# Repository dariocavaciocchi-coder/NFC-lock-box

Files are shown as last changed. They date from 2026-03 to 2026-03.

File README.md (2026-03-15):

# NFC-lock-box

Description:

My project is a lock box that uses rfid/NFC technology to lock and unlock it. It also has an LED to show whether it is locked or unlocked. All you have to do is tap the accepted card and the servo moves to unlock it, remove the lid, take stuff out or put stuff in, close it and tap the card again and the servo will lock the box. I made this project so I could store my most delicate items, without the risk of other people breaking them, as it has happened multiple times before (not on purpose).

Struggles:

I had a few struggles while making this project, but I will only talk about the big one, as I don’t want to bore you. I found it very hard to find an effective way to lock and unlock the box effectively, so much so that I changed the mechanism multiple times. At first, I had it to where a servo arm would go in a hole with a wedge and would move to lock/unlock but realised it would be hard to track the circular motion inside that hole, so then I thought of doing a linear locking mechanism. I came up with many ideas, but decided to go with a rack and pinion, as I thought that would be the easiest to implement in the box. I found a template for a rack and pinion online and modified it, so it could fit into the design of my box.

BOM:

A more detailed BOM can be found in the BOM folder

* Xiao RP2040 module X1
* RC522 module set X1
* SG90 servo motor X1
* 3D printed box X1
* M3 Headset inserts X6
* M3 4mm spacer X8
* PCB X1
* LED X1
* 330ohm resistor X1
* 100nF ceramic capacitor X1
* 100microF electrolytic capacitor X1
* 2.54mm pin header X3
* M3 12mm screws X4
* M3 6mm screws X2

Images:

More images can be found in the images folder

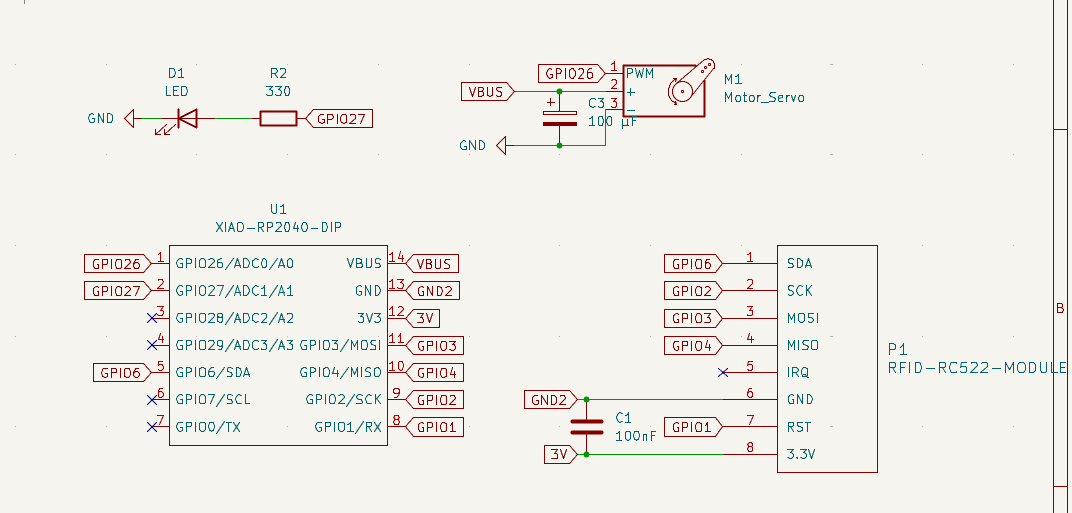
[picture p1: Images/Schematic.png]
Schematic


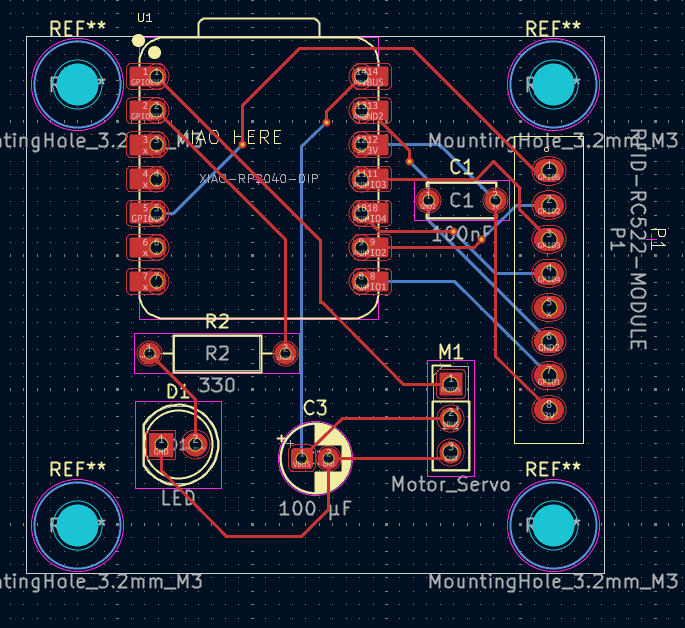
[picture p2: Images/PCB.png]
PCB


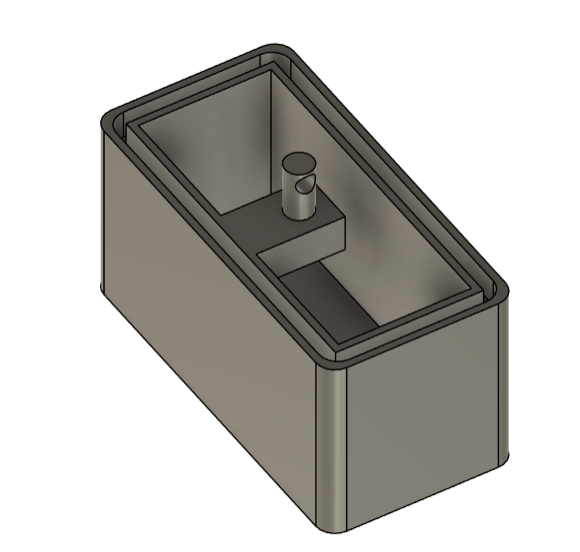
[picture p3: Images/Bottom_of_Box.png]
Bottom Case

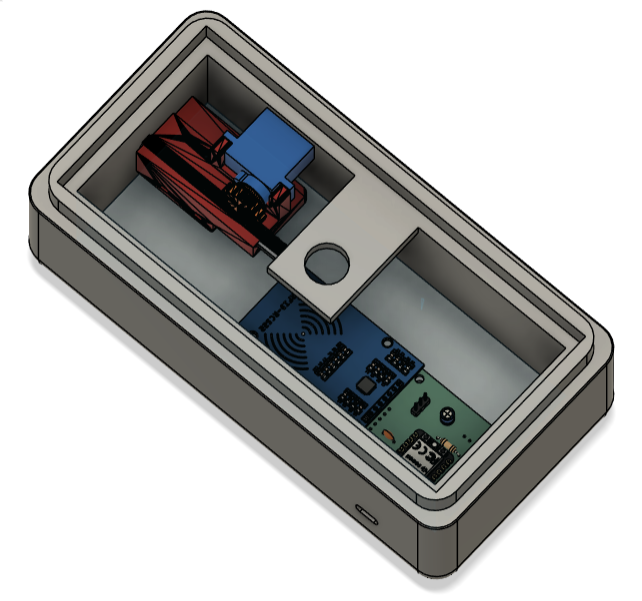
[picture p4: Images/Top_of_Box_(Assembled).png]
Top Case

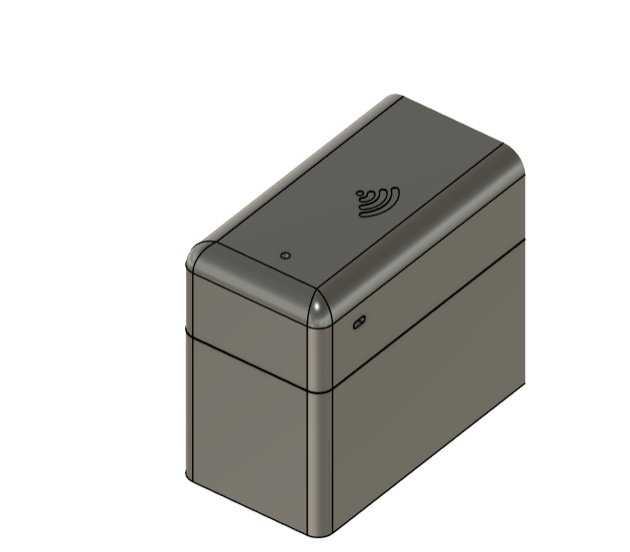
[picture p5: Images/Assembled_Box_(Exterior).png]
Assembled


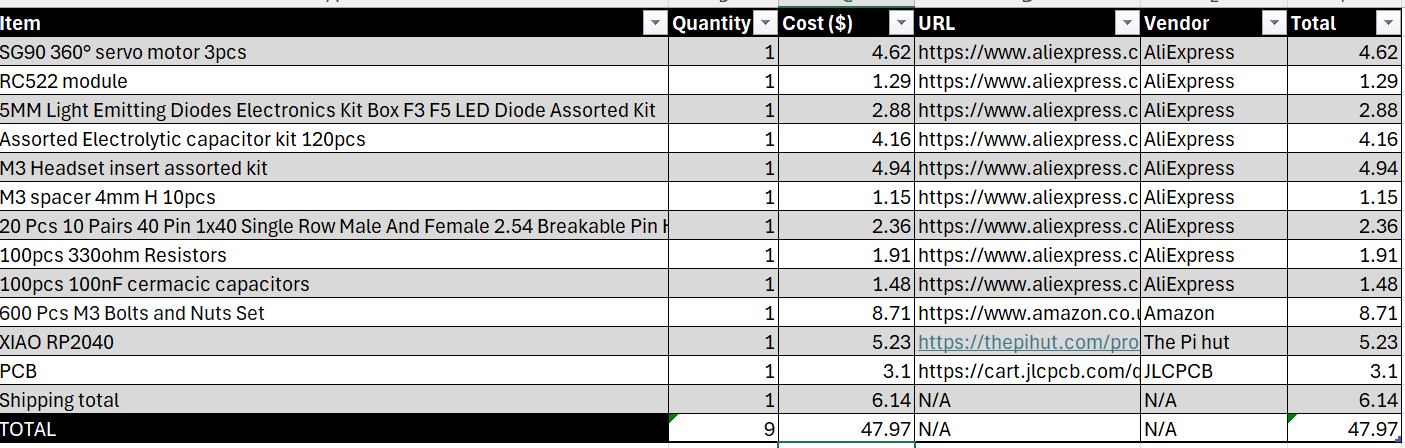
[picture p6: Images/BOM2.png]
BOM


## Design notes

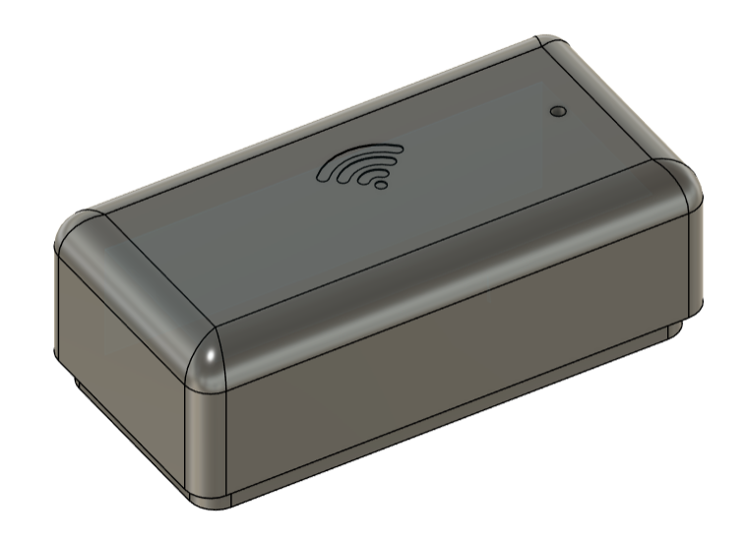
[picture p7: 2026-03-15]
Images/Top_of_Box_(Top).png

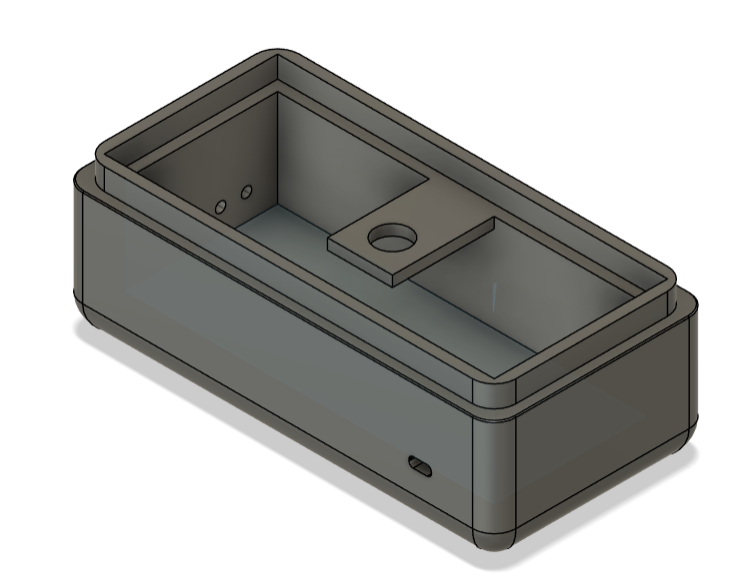
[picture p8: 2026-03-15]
Images/Top_of_Box_(Bottom).png

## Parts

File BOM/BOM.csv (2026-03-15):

Item | Quantity | Cost ($) | URL | Vendor | Total
SG90 360° servo motor 3pcs | 1 | 4.62 | https://www.aliexpress.com/item/1005005310063582.html?curPageLogUid=5EMKYWtYPEn4 | AliExpress | 4.62
RC522 module | 1 | 1.29 | https://www.aliexpress.com/item/1005006441061112.html?curPageLogUid=9xwa73kRGVRp | AliExpress | 1.29
5MM Light Emitting Diodes Electronics Kit Box F3 F5 LED Diode Assorted Kit | 1 | 2.88 | https://www.aliexpress.com/item/1005004543292837.html?curPageLogUid=vBeAjtTDarnR | AliExpress | 2.88
Assorted Electrolytic capacitor kit 120pcs | 1 | 4.16 | https://www.aliexpress.com/item/1005005661484224.html?curPageLogUid=ZUkhXYdLh8eC | AliExpress | 4.16
M3 Headset insert assorted kit | 1 | 4.94 | https://www.aliexpress.com/item/1005006472962973.html?curPageLogUid=ni6CXoPvNdtc | AliExpress | 4.94
M3 spacer 4mm H 10pcs | 1 | 1.15 | https://www.aliexpress.com/item/1005006915134966.html?curPageLogUid=MaqOvrXhgtMa | AliExpress | 1.15
20 Pcs 10 Pairs 40 Pin 1x40 Single Row Male And Female 2.54 Breakable Pin Header PCB Connector Strip | 1 | 2.36 | https://www.aliexpress.com/item/1005008559565009.html?curPageLogUid=BqjJbkfmWVMf | AliExpress | 2.36
100pcs 330ohm Resistors | 1 | 1.91 | https://www.aliexpress.com/item/1005003923602966.html?curPageLogUid=jXFSVmhfiauj | AliExpress | 1.91
100pcs 100nF cermacic capacitors | 1 | 1.48 | https://www.aliexpress.com/item/1005002290441861.html?curPageLogUid=19AxGaqwAapf | AliExpress | 1.48
600 Pcs M3 Bolts and Nuts Set | 1 | 8.71 | https://www.amazon.co.uk/KOXXIAMOQ-Washers-Mechanical-Fastener-Assortment/dp/B0CJ6L82T8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 | Amazon | 8.71
XIAO RP2040 | 1 | 5.23 | https://thepihut.com/products/seeed-xiao-rp2040 | The Pi hut | 5.23
PCB | 1 | 3.1 | https://cart.jlcpcb.com/quote?spm=Jlcpcb.Homepage.1006&spm=Jlcpcb.Homepage.1006 | JLCPCB | 3.1
Shipping total | 1 | 6.14 | N/A | N/A | 6.14
TOTAL | 9 | 47.97 | N/A | N/A | 47.97

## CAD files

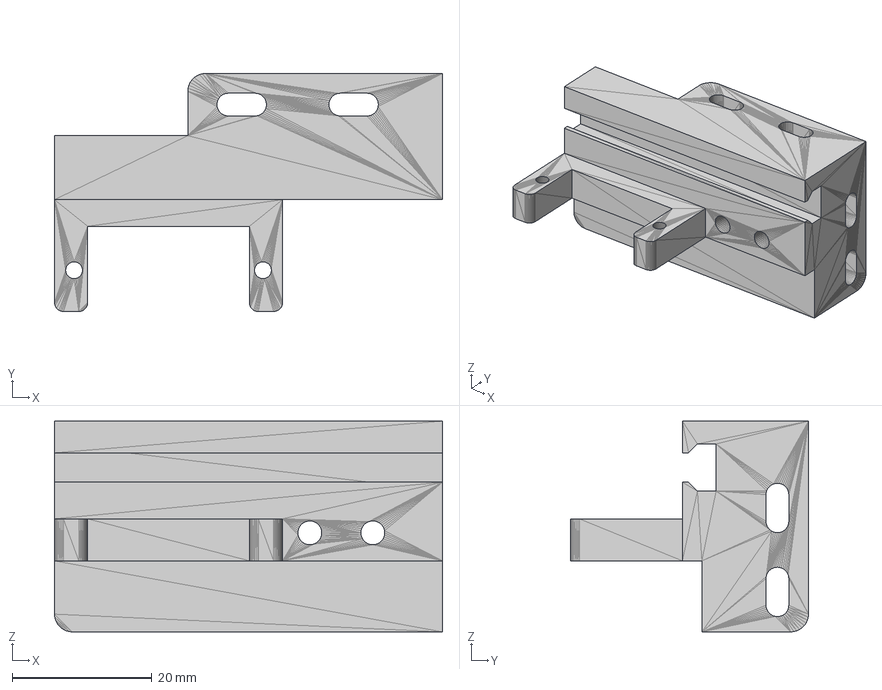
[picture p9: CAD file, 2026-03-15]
CAD/Motor_Bracket_Mini_Version.step
55.5 x 34.0 x 30.1 mm

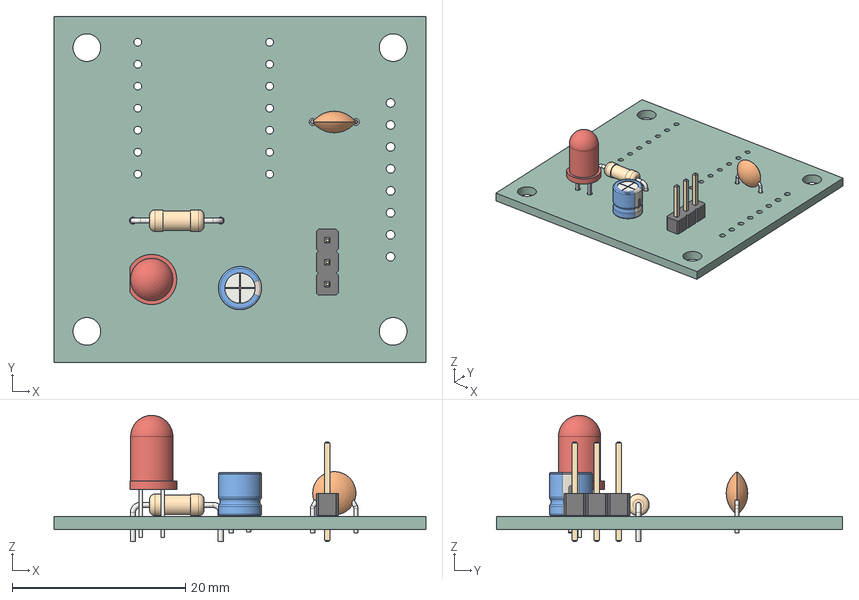
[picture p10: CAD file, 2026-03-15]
CAD/PCB.step
43.0 x 40.0 x 14.6 mm
PinHeader_1x03_P2.54mm_Vertical
LED_D5.0mm
C_Disc_D5.0mm_W2.5mm_P5.00mm
R_Axial_DIN0207_L6.3mm_D2.5mm_P10.16mm_Horizontal
CP_Radial_D5.0mm_P2.00mm
Lock box_PCB

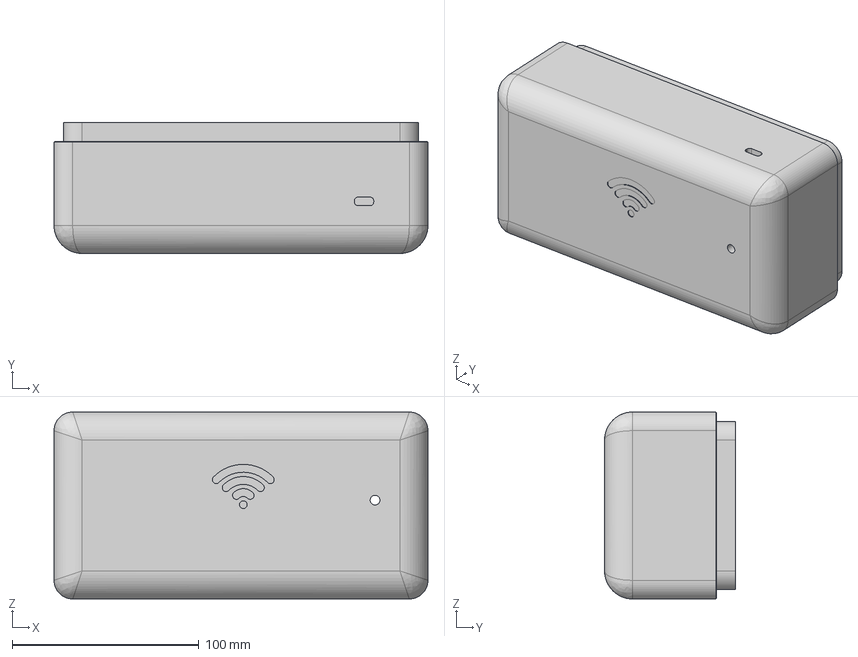
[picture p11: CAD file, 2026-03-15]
CAD/Top of box.step
200.0 x 70.0 x 100.0 mm

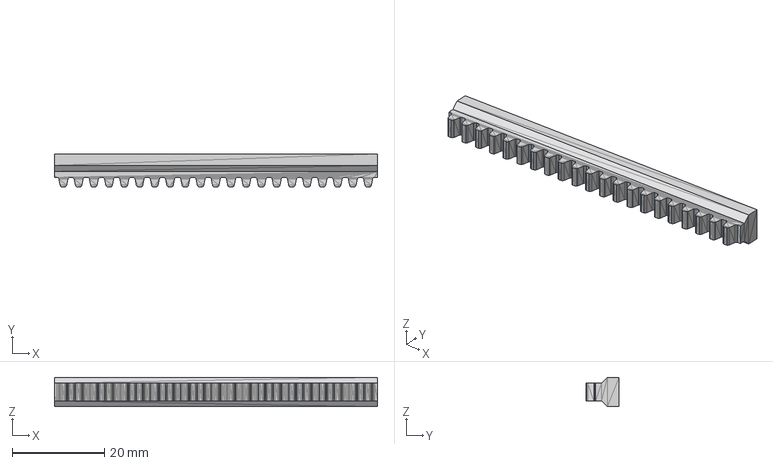
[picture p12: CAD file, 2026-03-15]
CAD/Pusher_75mm_Long.step
70.0 x 7.20 x 6.35 mm

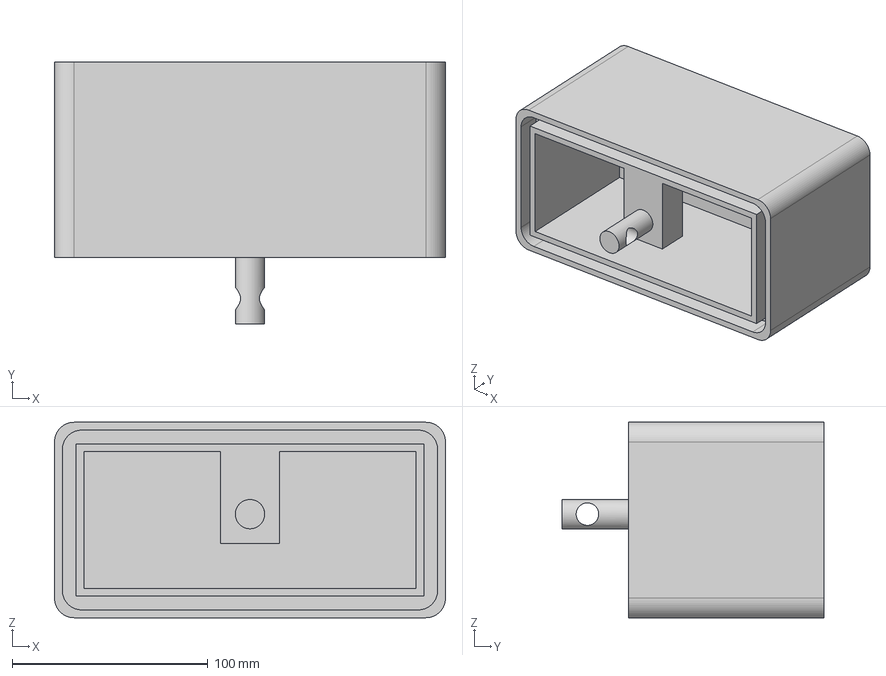
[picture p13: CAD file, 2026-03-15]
CAD/Bottom of box.step
200.0 x 134.0 x 100.0 mm

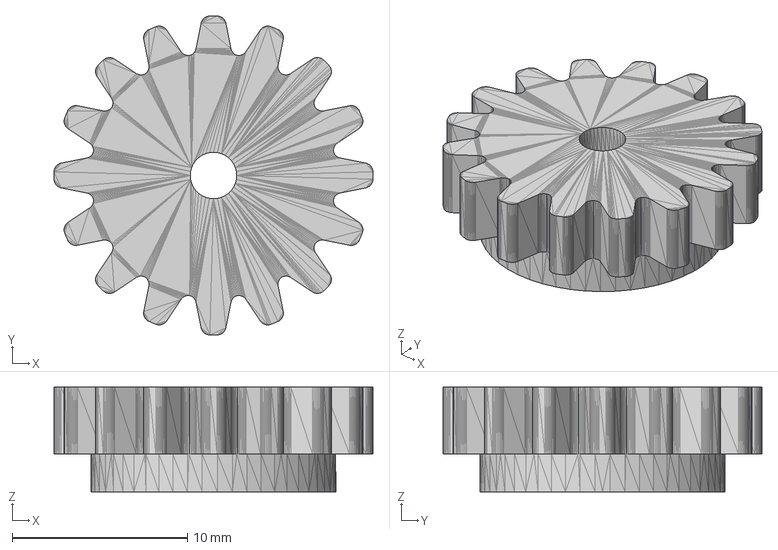
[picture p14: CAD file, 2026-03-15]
CAD/Pinion_Gear_Mini_Version.step
18.2 x 18.2 x 5.97 mm

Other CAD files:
CAD/Bottom of box.f3d
CAD/Motor_Bracket_Mini_Version.f3d
CAD/Pinion_Gear_Mini_Version.f3d
CAD/Pusher_75mm_Long.f3d

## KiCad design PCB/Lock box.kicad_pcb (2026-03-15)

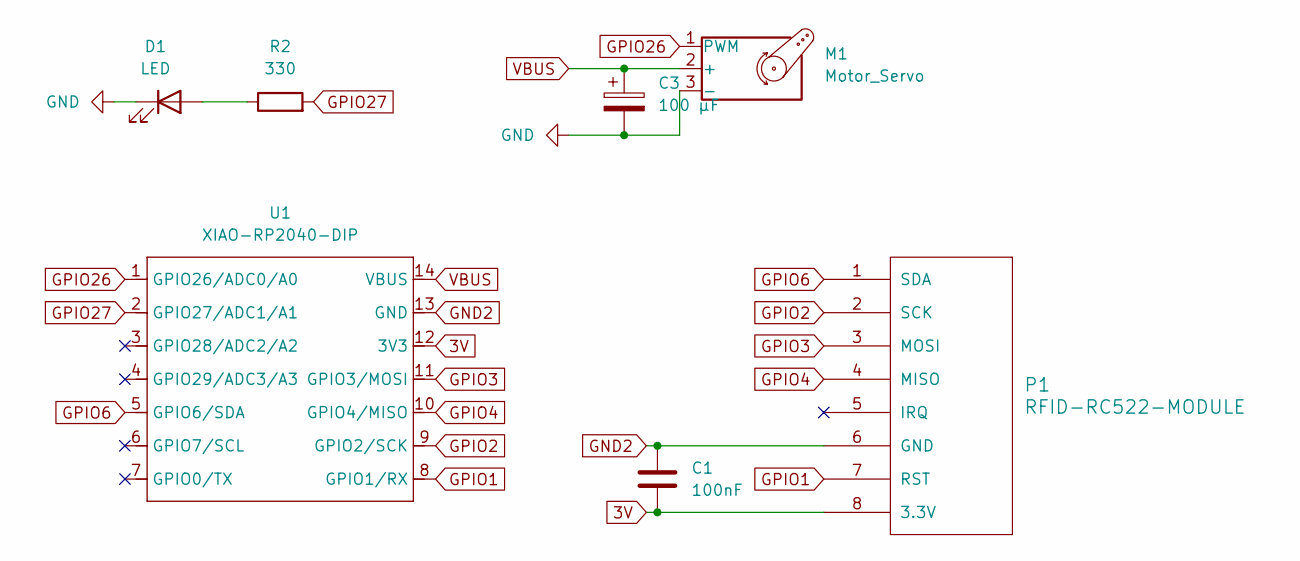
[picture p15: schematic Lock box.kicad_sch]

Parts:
C1: 100nF; C_Disc_D5.0mm_W2.5mm_P5.00mm
C3: 100 µF; CP_Radial_D5.0mm_P2.00mm
D1: LED; LED_D5.0mm
M1: Motor_Servo; PinHeader_1x03_P2.54mm_Vertical
P1: RFID-RC522-MODULE; RC522_Module
R2: 330; R_Axial_DIN0207_L6.3mm_D2.5mm_P10.16mm_Horizontal
U1: XIAO-RP2040-DIP

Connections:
3V: C1.2, P1.8 (3.3V), U1.12 (3V3)
GND: C3.2, D1.1 (K), M1.3 (-)
GND2: C1.1, P1.6 (GND), U1.13 (GND)
GPIO1: P1.7 (RST), U1.8 (GPIO1/RX)
GPIO2: P1.2 (SCK), U1.9 (GPIO2/SCK)
GPIO3: P1.3 (MOSI), U1.11 (GPIO3/MOSI)
GPIO4: P1.4 (MISO), U1.10 (GPIO4/MISO)
GPIO6: P1.1 (SDA), U1.5 (GPIO6/SDA)
GPIO26: M1.1 (PWM), U1.1 (GPIO26/ADC0/A0)
GPIO27: R2.2, U1.2 (GPIO27/ADC1/A1)
unnamed: D1.2 (A), R2.1
VBUS: C3.1, M1.2 (+), U1.14 (VBUS)

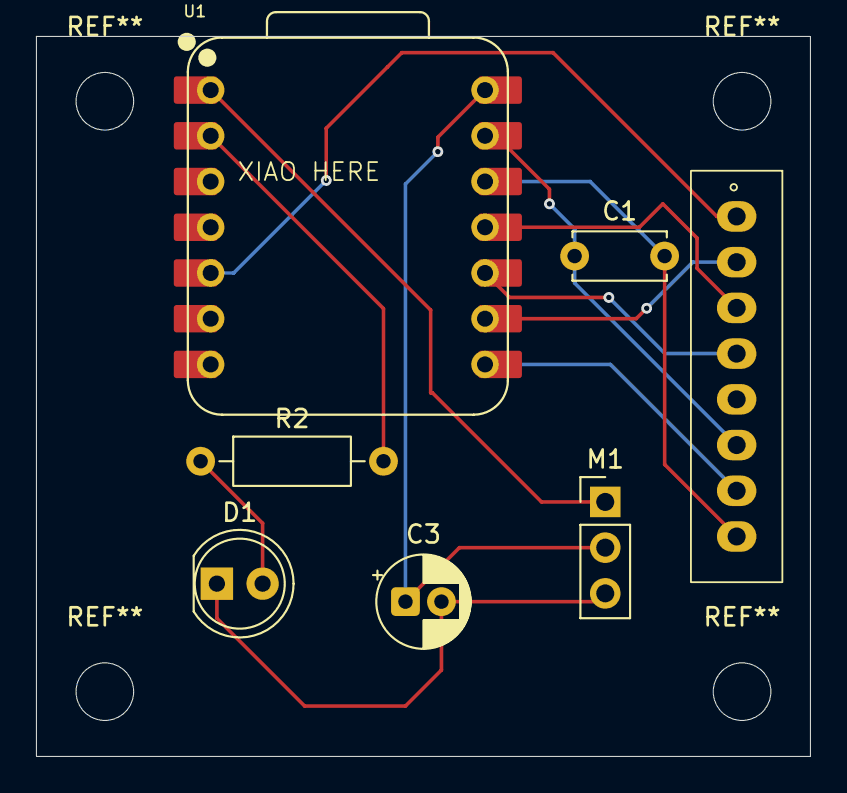
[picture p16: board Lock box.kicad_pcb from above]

Board: 2 copper layers, 43.0 x 40.0 mm, 7 parts (0 on the bottom side), 12 nets.

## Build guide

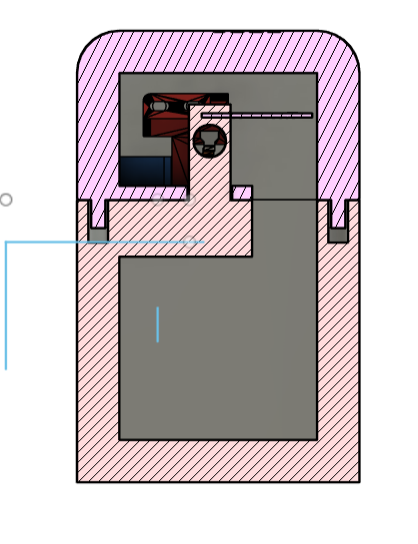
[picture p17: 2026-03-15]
Images/Assembled_Box_(Intersection).png

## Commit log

2026-03-15 Added all my files
    [BOM.csv, BOM.xlsx, Bottom of box.f3d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]
2026-03-15 Fixed BOM and symbols on readme
    [BOM.csv, BOM.xlsx]
